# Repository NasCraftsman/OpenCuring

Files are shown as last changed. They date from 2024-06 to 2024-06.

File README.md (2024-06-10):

# OpenNixie 

</a>
</a>
</a>

Democratizing manufacturing tools is the only way to bring technological design closer to everyone. OpenCuring is the first open source resin curing machine. The first in a series of completely open manufacturing tools that will allow anyone to have their own maker lab at home.

To make this machine available to everyone, simple and affordable components have been used, such as a single and cheap PCB, a completely standard 28BYJ-48 stepper motor and an SSD1306 OLED screen. Additionally, all pieces are fully printable.

On the other hand, OpenCuring has a completely modular design, so the user can add new curing arms as needed.

There is no excuse to get your hands dirty creating!

Some of the features that the OpenCuring platform includes are:

- Wifi and BLE connected
- Modular design: it can be adapted to the user needs 
- USB Type-C for power and programming
- Up to 3A at 5V 
- 1 general pourpose button 
- 1 general pourpose potentiometer 
- 1 OLED display 
- 1 stepper motor
  
<a href="https://www.pcbway.com/project/shareproject/Open_Resin_Curing_Machine_8a6f1ecd.html">PCB from PCBWay</a>

## Multi Board Architecture

OpenCuring integrates two different pcbs: 

- <strong>Control PCB:</strong> this system includes all the user interfaces such as the OLED display, the butons and potentiometer, the USB port and all the integrated control systems. 
- <strong>Branch PCB:</strong>  this system includes the UV LEDs 

OpenCuring has been designed as a modular platform. This means that the control PCB can be connected to any UV LED PCB to adapt the system to the user's needs, playing with the wavelength and power emitted. On the other hand, the PCBs of the branches will be connected in series, allowing the user to expand the number of UV arms by adapting the system to their needs.

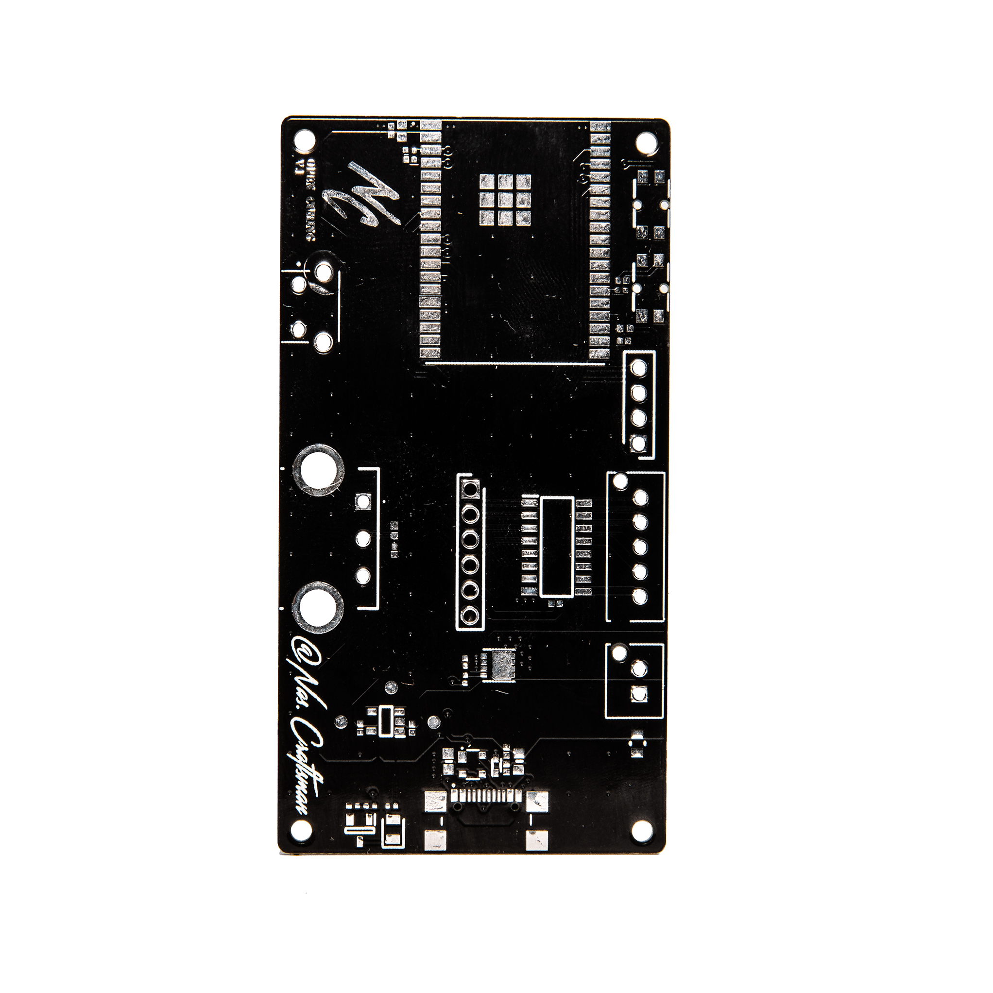
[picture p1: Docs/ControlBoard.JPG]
</a>
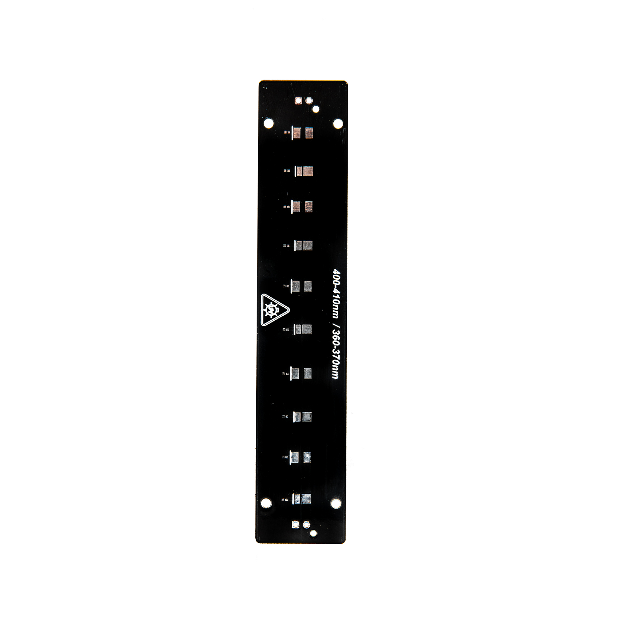
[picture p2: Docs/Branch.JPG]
</a>

## Warning

OpenCuring uses 405nm UV power LEDs, which can be hazardous to human eyesight. Please wear protective glasses or stay away from the system while the curing process is running.

## GPIOs

Function|  GPIO  | Mode
--------| ------ | -----
USB_LED | GPIO26 | Output
BUTTON  | GPIO15 | Input
POT     | GPIO36 | Input
I2C_SDA | GPIO21 | Output/Input
I2C_SCL | GPIO22 | Output
UV      | GPIO25 | Output
STEP_A1 | GPIO27 | Output
STEP_A2 | GPIO14 | Output
STEP_A3 | GPIO33 | Output
STEP_A4 | GPIO32 | Output

- The USB LED is used to indicate that a correct power source has been connected
- The button is used to start the curing process.
- The potentiometer is used to select the curing time.
- The UV pin activates a power mosfet to turn on the UV power LEDs
- STEP A1 to A4 are the control lines of the stepper motor
- The I2C bus controls the OLED display

## Board overview C3T 

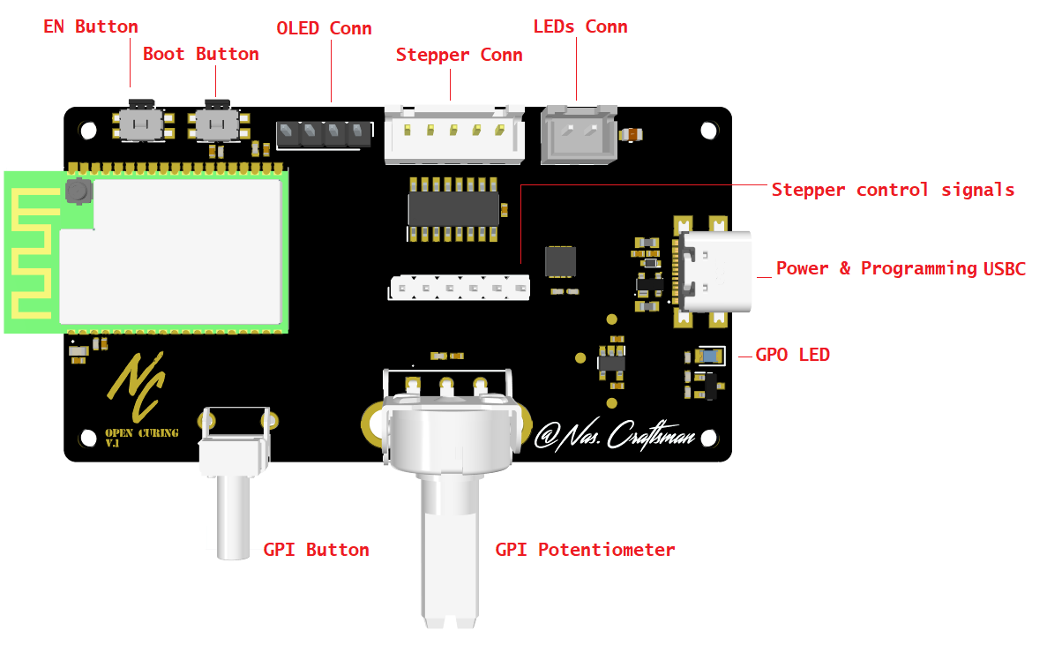
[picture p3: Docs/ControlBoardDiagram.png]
</a>

## Flashing firmware to the ESP32 

- Press and hold BOOT button while press and release EN button, then release BOOT button to enter in BOOT mode
- You can use the USB-C directly to programm the device

## Media

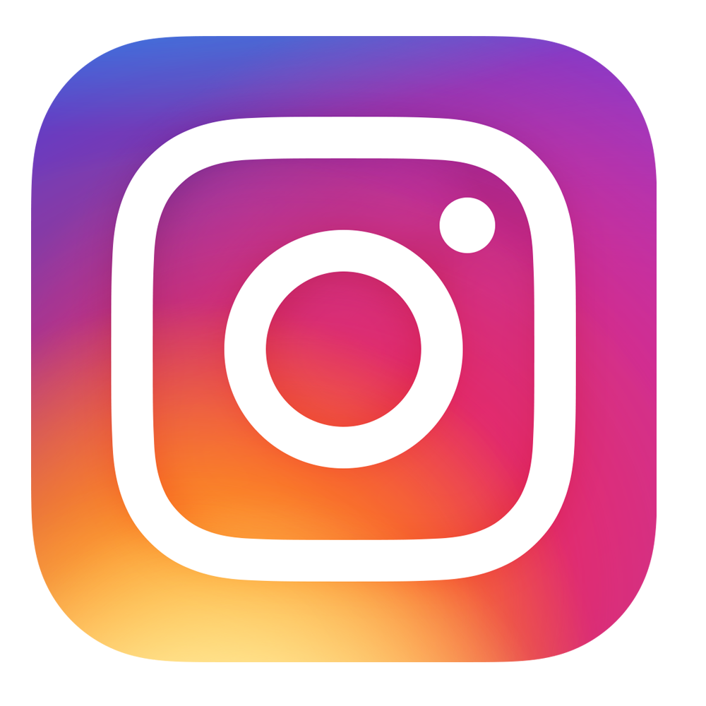
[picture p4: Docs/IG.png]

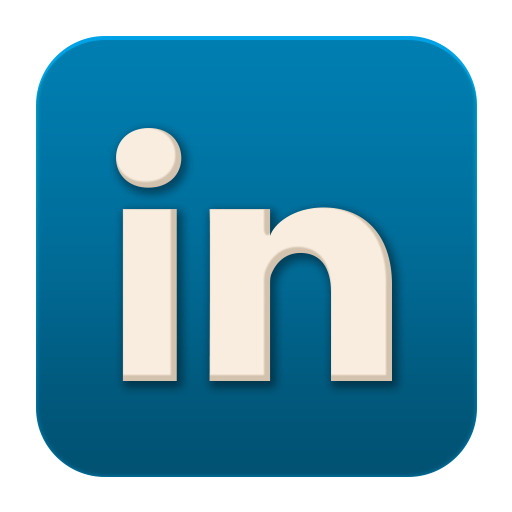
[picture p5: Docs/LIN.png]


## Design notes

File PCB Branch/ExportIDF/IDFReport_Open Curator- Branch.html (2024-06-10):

Altium customize

# IDF File Translation Report

Date: | | 26/04/2024
Time: | | 18:11:25
Elapsed Time: | | 00:00:00
PCB Filename | : | F:\NASIB\INGENIERIA\PROYECTOS\4-OPEN CURATOR\BRANCH\Open Curator- Branch.PcbDoc
IDF Board Filename | : | F:\NASIB\INGENIERIA\PROYECTOS\4-OPEN CURATOR\BRANCH\Project Outputs for Open Curator- Branch\ExportIDF\Open Curator- Branch.brd
IDF Library Filename | : | F:\NASIB\INGENIERIA\PROYECTOS\4-OPEN CURATOR\BRANCH\Project Outputs for Open Curator- Branch\ExportIDF\Open Curator- Branch.pro

Errors

Back to top

Warnings

Back to top

Save Warnings

Back to top

Save Errors

Back to top

Export Warnings

Back to top

Export Errors

Back to top

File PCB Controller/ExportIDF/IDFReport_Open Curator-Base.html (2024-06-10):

Altium customize

# IDF File Translation Report

Date: | | 26/04/2024
Time: | | 18:04:49
Elapsed Time: | | 00:00:00
PCB Filename | : | F:\NASIB\INGENIERIA\PROYECTOS\4-OPEN CURATOR\BASE\Open Curator-Base.PcbDoc
IDF Board Filename | : | F:\NASIB\INGENIERIA\PROYECTOS\4-OPEN CURATOR\BASE\Project Outputs for Open Curator-Base\ExportIDF\Open Curator-Base.brd
IDF Library Filename | : | F:\NASIB\INGENIERIA\PROYECTOS\4-OPEN CURATOR\BASE\Project Outputs for Open Curator-Base\ExportIDF\Open Curator-Base.pro

Errors

Back to top

Warnings

Back to top

Save Warnings

Back to top

Save Errors

Back to top

Export Warnings

Back to top

Export Errors

Back to top

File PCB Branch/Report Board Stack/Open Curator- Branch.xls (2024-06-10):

Board Stack Report
Stack Up |  | Layer Stack
Layer | Board Layer Stack | Name | Material | Thickness | Constant
1 |  | Top Paste
2 |  | Top Overlay
3 |  | Top Solder | Solder Resist | 0,005mm | 4,2
4 |  | Top Layer | Copper | 0,035mm
5 |  | Core | FR-4 | 1,000mm | 4,29
6 |  | Bottom Layer | Copper | 0,035mm
7 |  | Bottom Solder | Solder Resist | 0,005mm | 4,2
8 |  | Bottom Overlay
9 |  | Bottom Paste
 | Height : 1,080mm

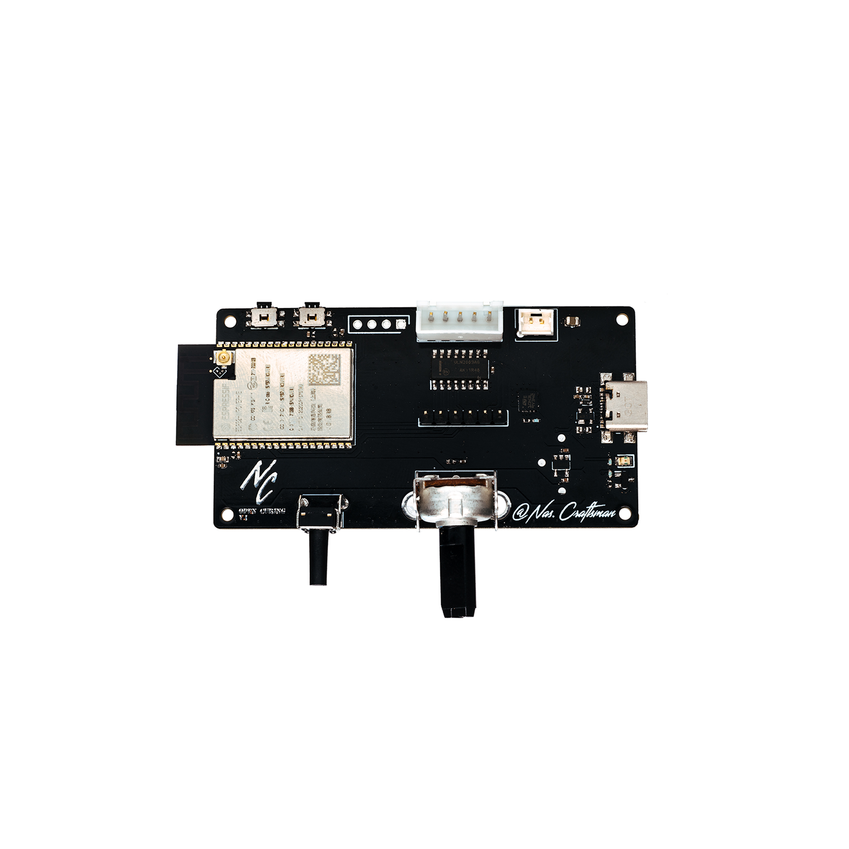
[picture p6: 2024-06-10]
Docs/OpenCuringv11.JPG

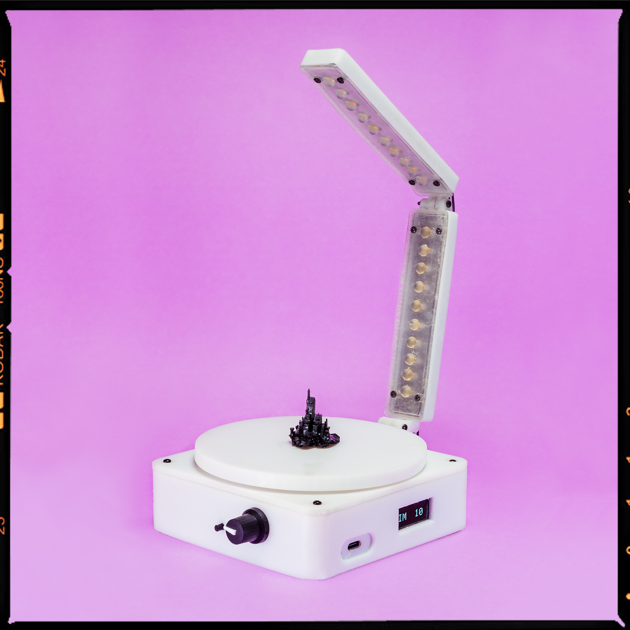
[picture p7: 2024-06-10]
Docs/_DSC4096-Edit.jpg

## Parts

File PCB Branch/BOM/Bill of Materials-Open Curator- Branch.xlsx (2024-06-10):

Designator | Value | Description | Quantity | Part Number | Manufacturer | DNP
J100, J101 |  | Connector | 2 | B2B-XH-AM(LF)(SN) | JST (JAPAN SOLDERLESS TERMINALS)
L100, L101, L102, L103, L104 |  | SMD UV Clear Non-Diff 405nm | 5 | VLMU3100-GS08 | Vishay
L105, L106, L107, L108, L109 |  | SMD UV Clear Non-Diff 405nm | 5 | 153283367A212 | Wurth Elektronik
R100, R101, R102, R103, R104 | 60 | SMD 59 Ohms 62.5 mW 0402 1% | 5 | RC0402FR-0759RL | Yageo
R105, R106, R107, R108, R109 | 24 | SMD 24 Ohms 62.5 mW 0402 5% | 5 | RC0402JR-0724RL | Yageo

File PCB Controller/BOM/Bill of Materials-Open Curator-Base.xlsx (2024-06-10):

Designator | Value | Description | Quantity | Part Number | Manufacturer | DNP
C100 | 10nF | 0.01 uF 16 VDC 20% 0402 X7R | 1 | GRM155R71C103MA01D | Murata
C101, C102, C104, C105, C109, C110, C112, C113 | 100nF | CAP, MLCC, 0402/1005, 25V, X7R, | 8 | GRM155R71E104KE14D | Murata
C103 | 22uF | CAP CER 22UF 6.3V X5R 0603 | 1 | GRM188R60J226MEA0D | Murata
C106, C107 | 1uF | 1.0uF 16V 10% 0402 X5R | 2 | GRM155R61C105KA12D | Murata
C108 | 22uF | 0805 35VDC 22uF 20% X5R 1.25mm | 1 | C2012X5R1V226M125AC | Murata
C111 | 4.7uF | 4.7uF 10V 20% 0402 X5R | 1 | GRM155R61A475MEAAD | Murata
D100 |  | ESD / TVS diode 12-pF, +/-5.5V, +/-30-kV ESD protection diode in 0402 and SOD-523 package | 1 | TPD1E10B06DYAR | Texas Instruments
D101 |  | LED | 1 | 597-3305-607F | Dialight
D102 |  | ESD Diode | 1 | PRTR5V0U2X | Nexperia
FB100, FB101 |  | Ferrite Bead, 2A @ 100MHz, 120ohms 25% | 2 | ILHB0603ER121V | Vishay
J100 |  | Connector | 1 | USB4110-GF-A | GCT (GLOBAL CONNECTOR TECHNOLOGY)
J101 |  | Connector | 1 | B2B-XH-AM(LF)(SN) | JST (JAPAN SOLDERLESS TERMINALS)
J102 |  | Connector | 1 | G800W302018EU | Amphenol Communications Solutions
J103 |  | Connector | 1 | B5B-XH-AM (LF)(SN) | JST (JAPAN SOLDERLESS TERMINALS)
J104 |  | Connector | 1 | PH1-04-UA | Adam Tech
P100 |  | Pot 12mm 5Kohm | 1 | P120K-F20BR5K | TT Electronics
Q100 |  | MOSFET N-channel 30 V 0.015 Ohm 9A STripFET V | 1 | STL10N3LLH5 | STMicroelectronics
Q102 |  | MOSFET (N-Channel) | 1 | NX7002AKVL | Nexperia
R100, R101, R108 | 100 | RES SMD 100 OHM 1% 1/16W 0402 | 3 | MCS04020D1000BE000 | Vishay
R102, R107, R110, R111 | 100k | 100 kOhms 62.5mW 0402 1% | 4 | RC0402FR-07100KL | Yageo
R103, R104 | 10k | RES SMD 10K OHM 1% 1/16W 0402 | 2 | SFR01MZPF1002 | Stackpole Electronics Inc
R105 | 1k | RES SMD 1K OHM 1% 1/16W 0402 | 1 | CRT0402-FZ-1001GST | Yageo
R106 | 22.1k | RES SMD 22.1K OHM 1% 1/16W 0402 | 1 | RT0402BRE0722K1L | Stackpole Electronics Inc
R109 | 47.5k | RES SMD 47.5K OHM 1% 1/16W 0402 | 1 | RN731ETTP4752F50 | Stackpole Electronics Inc
S100 |  | Connector | 1 | 2-1825027-0 | TE Connectivity
S101, S102 |  | button | 2 | 436331045822 | Wurth Elektronik
U100 |  | 700mA High Speed LDO Regulator | 1 | XC6210B332MR-G | Torex
U101 |  | Wi-Fi - 802.11 SMD Module ESP32-WROVER-IE, ESP32-D0WD-V3, 3.3V 64Mbit PSRAM, 16 MB SPI flash, IPEX connector | 1 | ESP32-WROVER-IE(M213EH2864UH3Q0) | Espressif Systems
U102 |  | DARLINGTON TRNS ARRY | 1 | ULN2003ADR2G | onsemi
U103 |  | USB to UART Bridge QFN24 | 1 | CP2102N-A02-GQFN24R | Silicon Labs

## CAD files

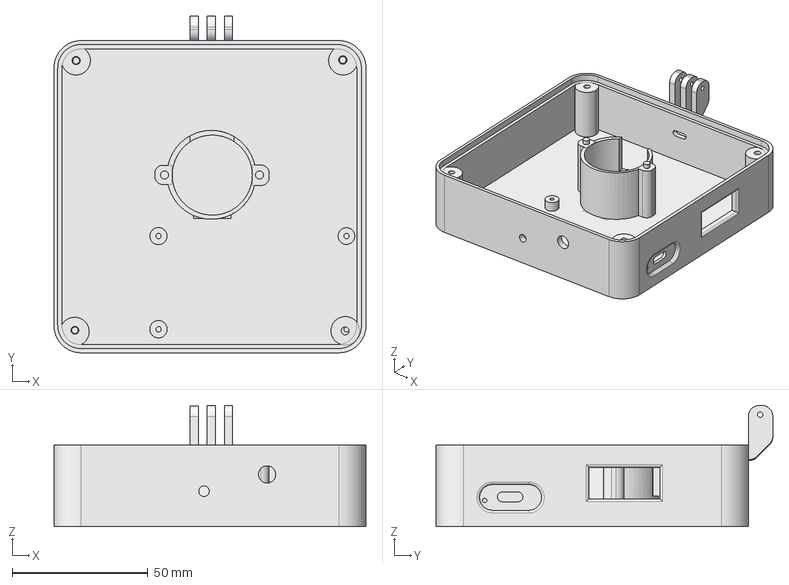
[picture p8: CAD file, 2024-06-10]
Case/Body.step
114.9 x 124.0 x 44.6 mm

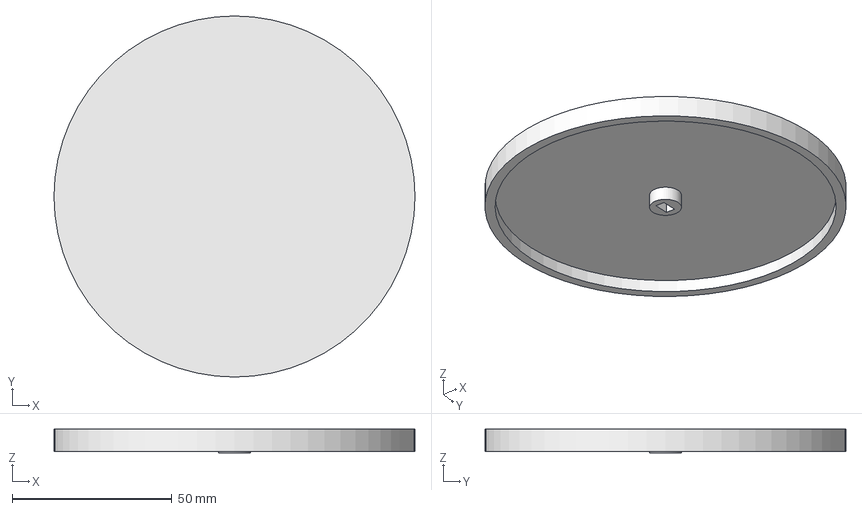
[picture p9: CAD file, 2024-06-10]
Case/Platform.step
112.8 x 112.8 x 7.40 mm

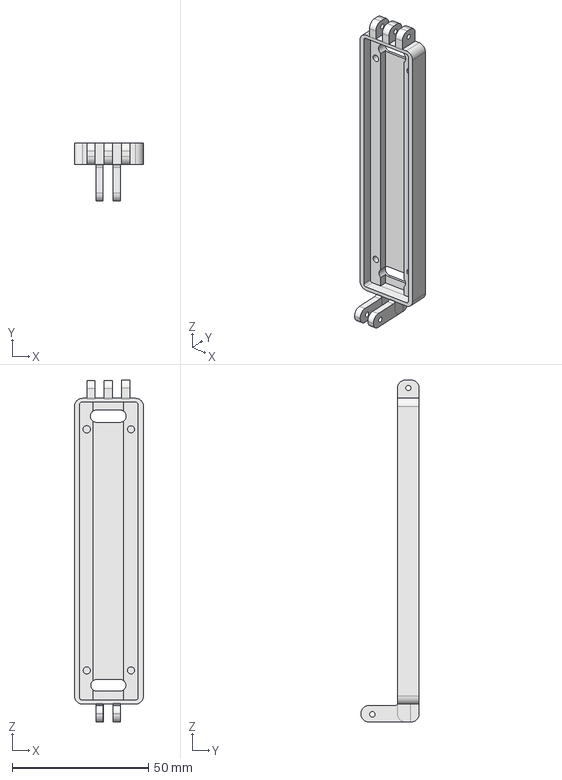
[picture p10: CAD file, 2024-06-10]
Case/Branch_Vertical_Base.step
25.4 x 21.5 x 125.7 mm

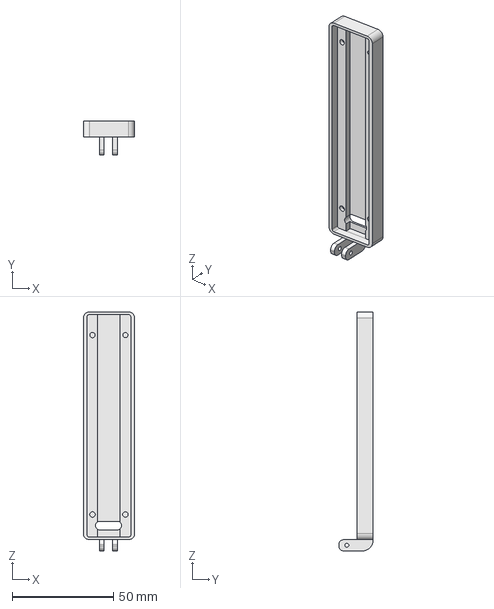
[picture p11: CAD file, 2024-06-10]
Case/Branch_Horizontal_Base.step
25.4 x 17.0 x 118.1 mm

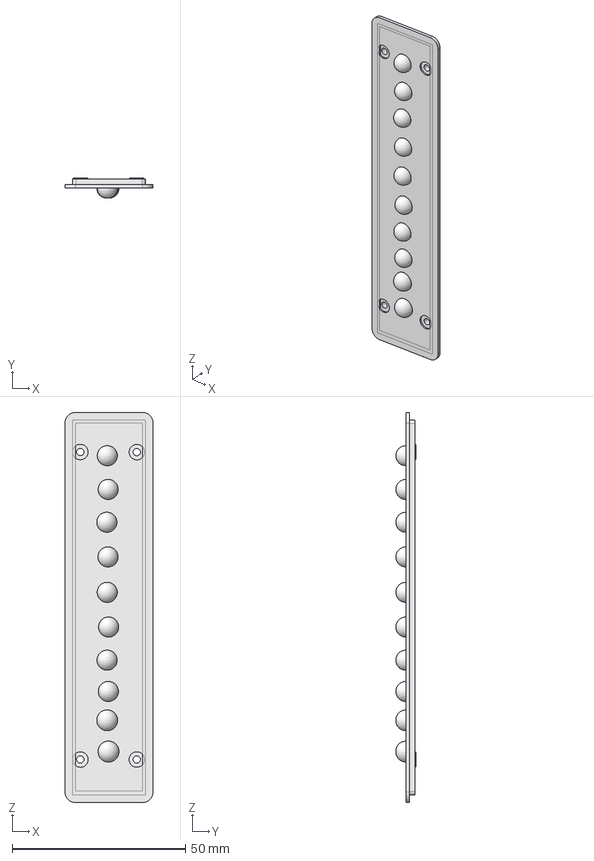
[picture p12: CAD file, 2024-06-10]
Case/Branch_Vertical_Lid.step
25.4 x 5.90 x 112.4 mm

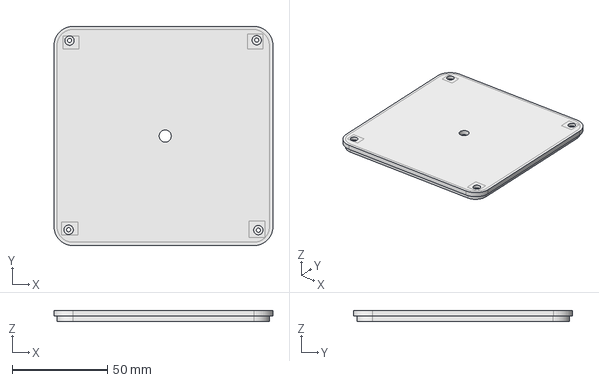
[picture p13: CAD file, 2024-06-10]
Case/Lid.step
114.9 x 115.0 x 6.00 mm

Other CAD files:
Case/Branch_Horizontal_Lid.step
PCB Branch/ExportSTEP/Open Curator- Branch.x_t

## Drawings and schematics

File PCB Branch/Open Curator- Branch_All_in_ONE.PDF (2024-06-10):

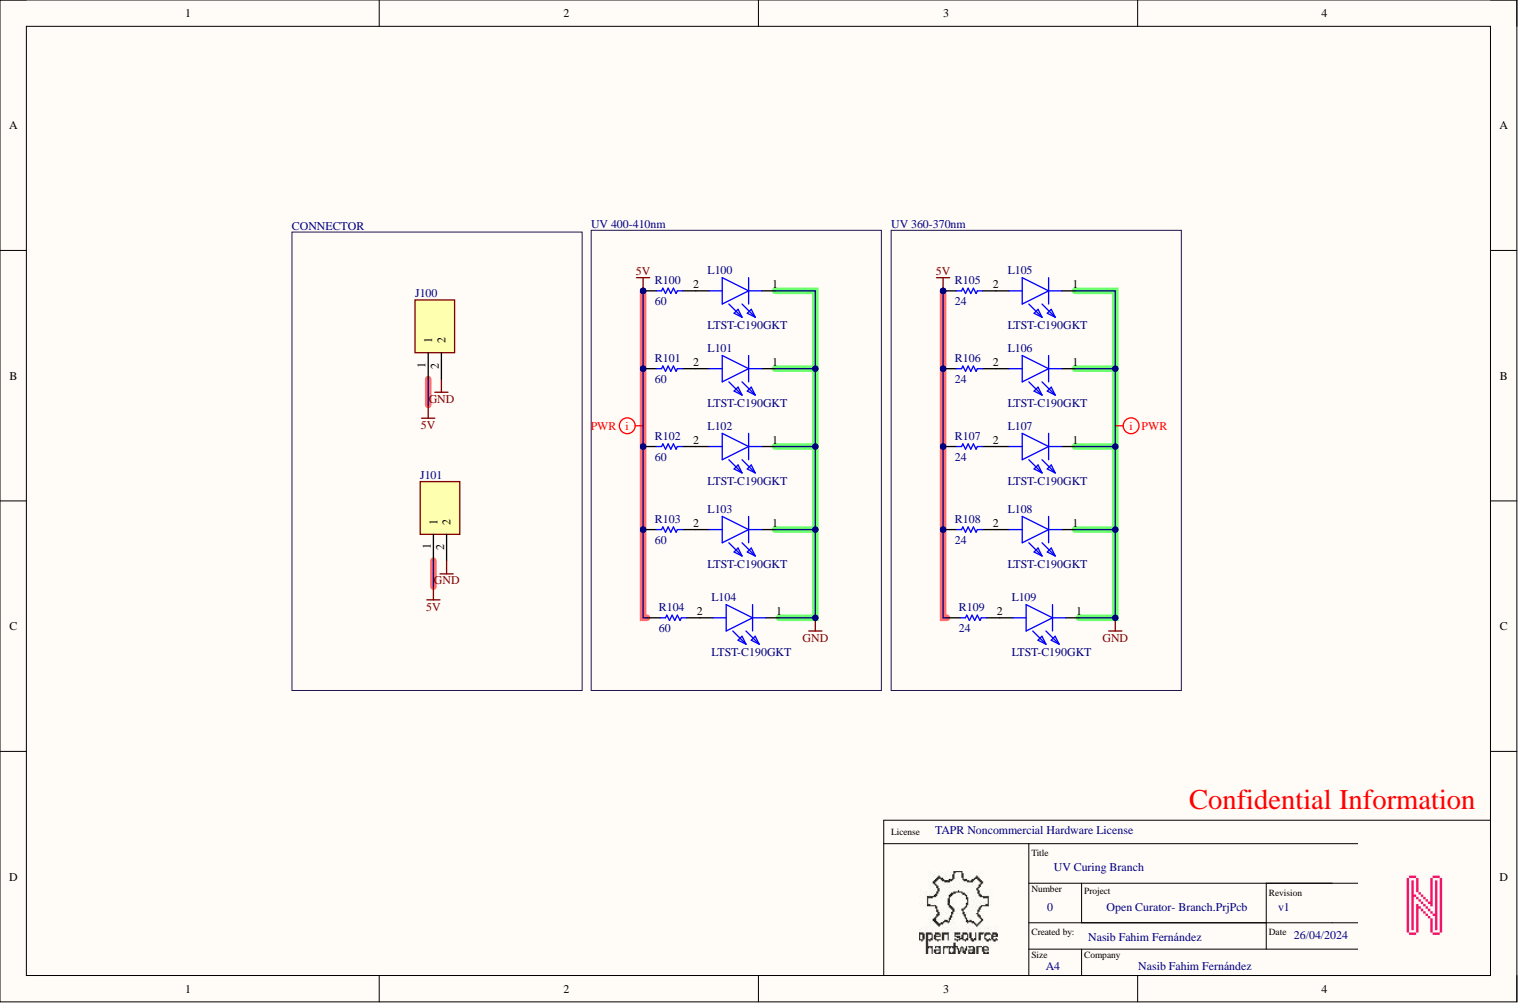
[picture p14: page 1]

Title UV Curing Branch

Number 0 | Project Open Curator- Branch.PrjPcb | Revision v1

Created by: Nasib Fahim Fernández | | Date 26/04/2024

Company

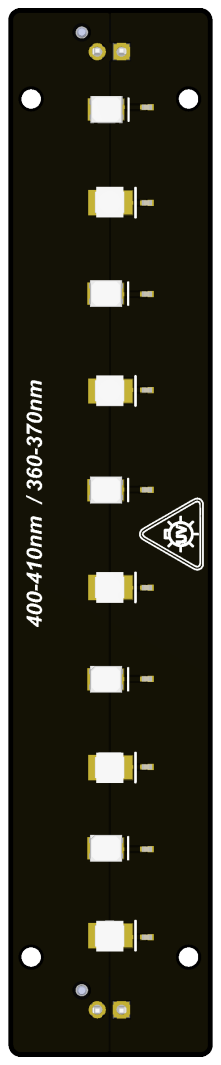
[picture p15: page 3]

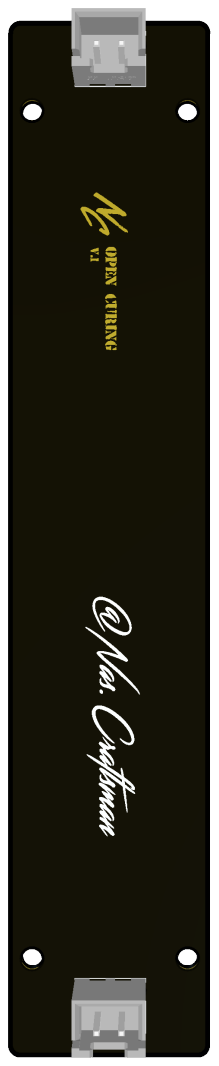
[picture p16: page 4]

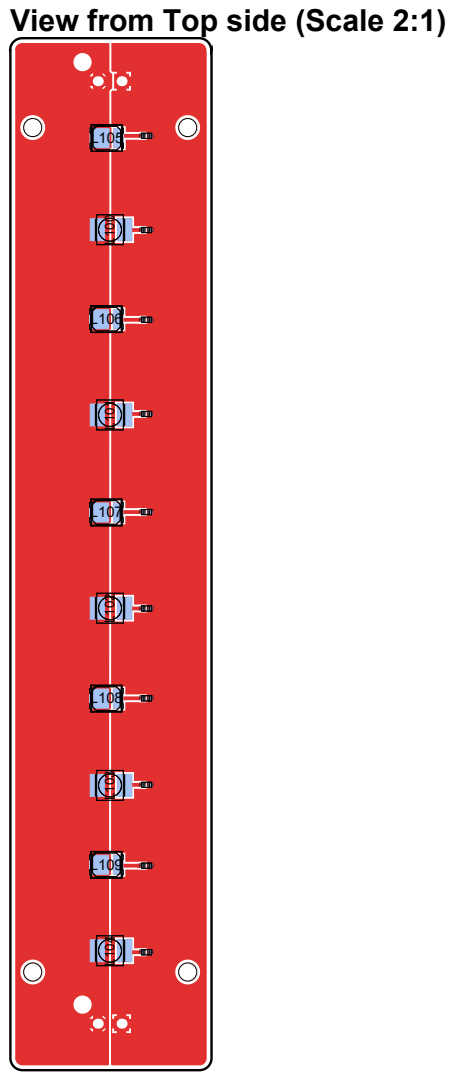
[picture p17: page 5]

View from Top side (Scale 2:1)

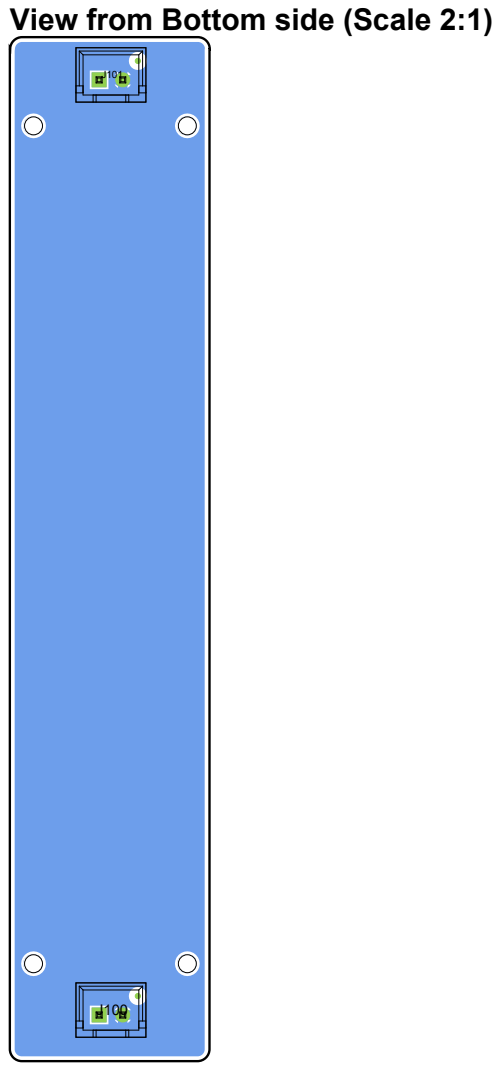
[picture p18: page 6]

View from Bottom side (Scale 2:1)

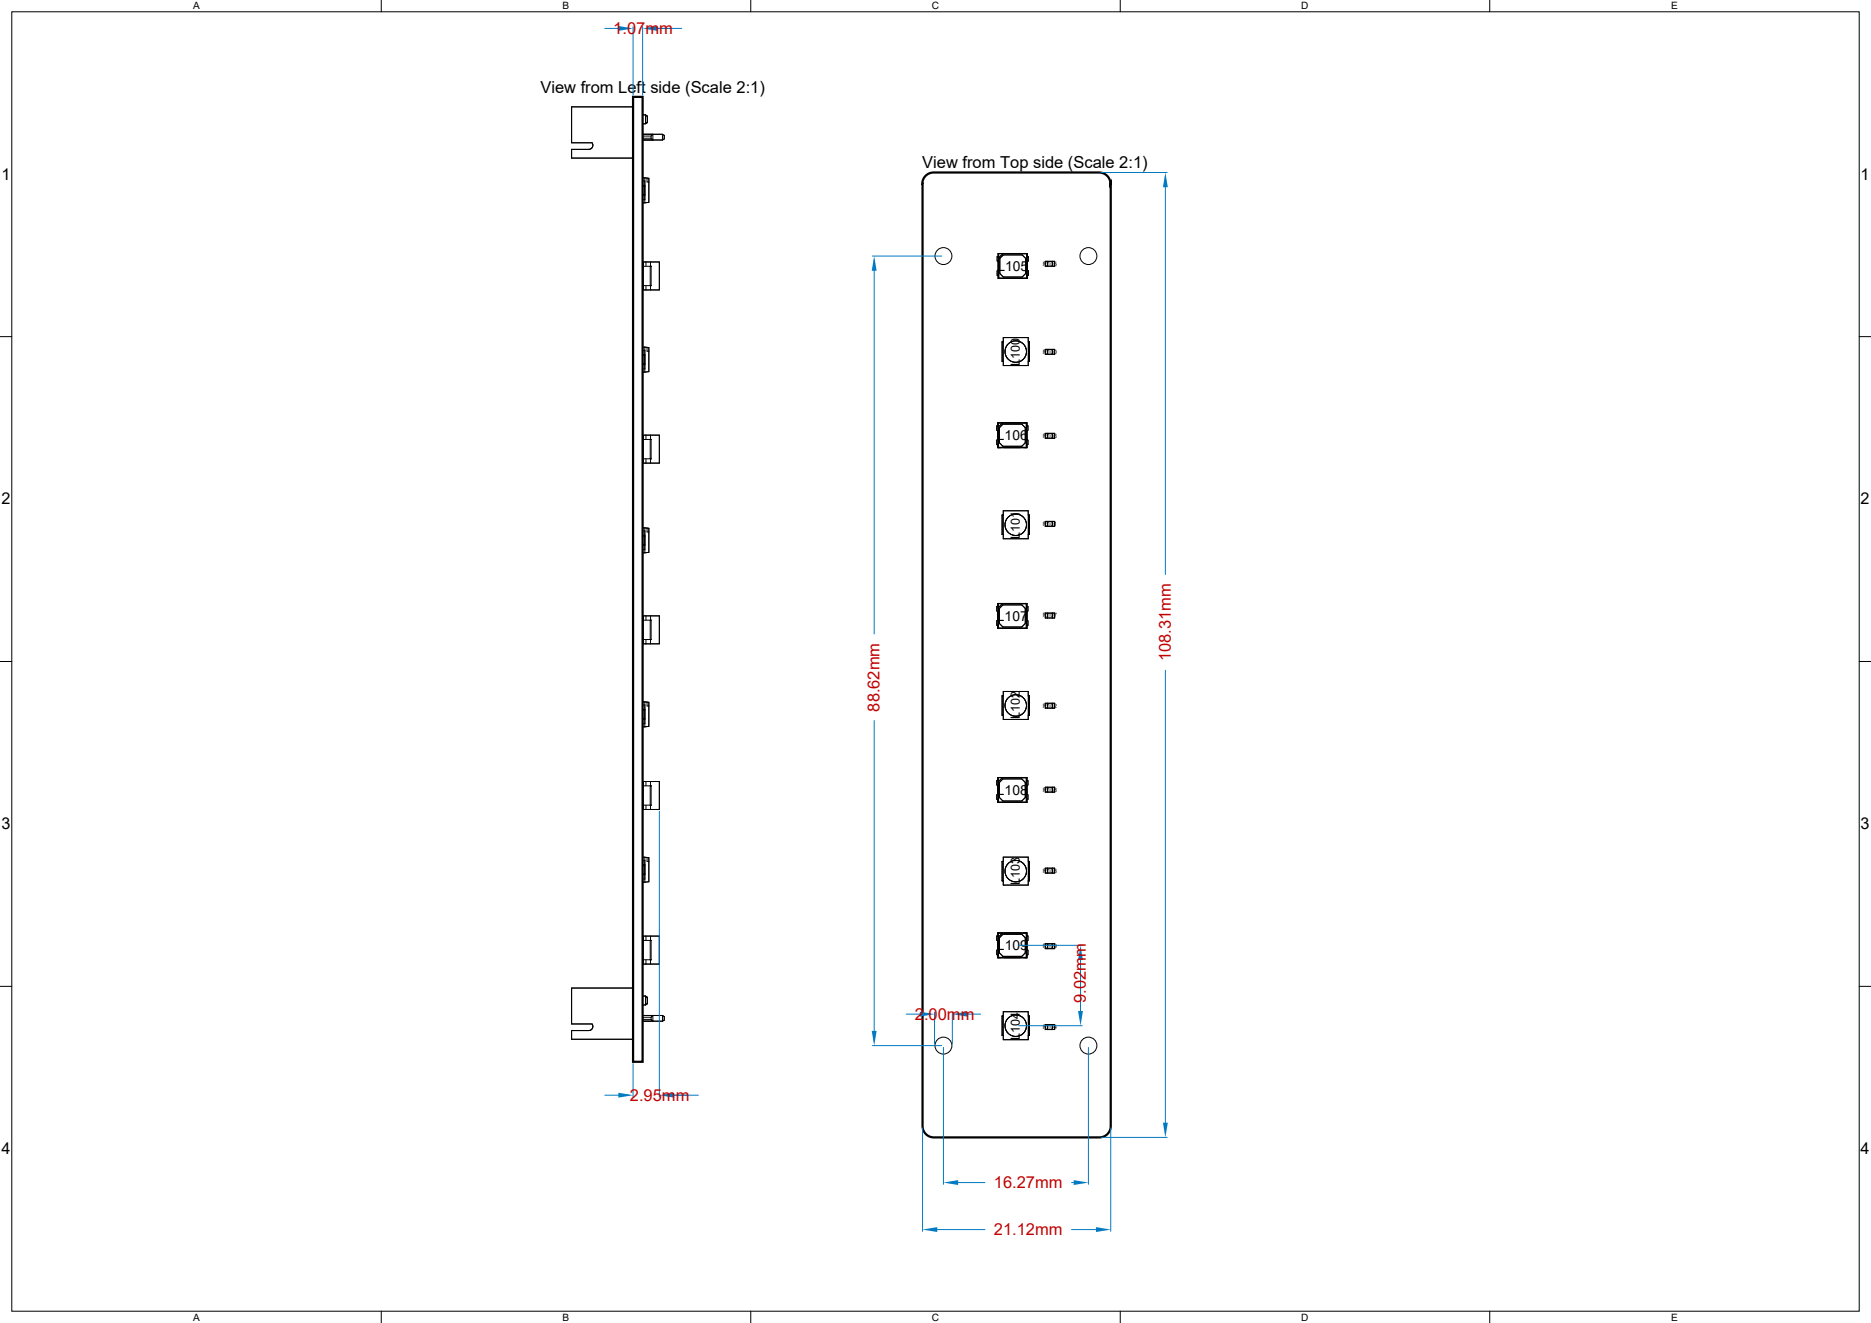
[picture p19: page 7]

View from Left side (Scale 2:1)

View from Top side (Scale 2:1)

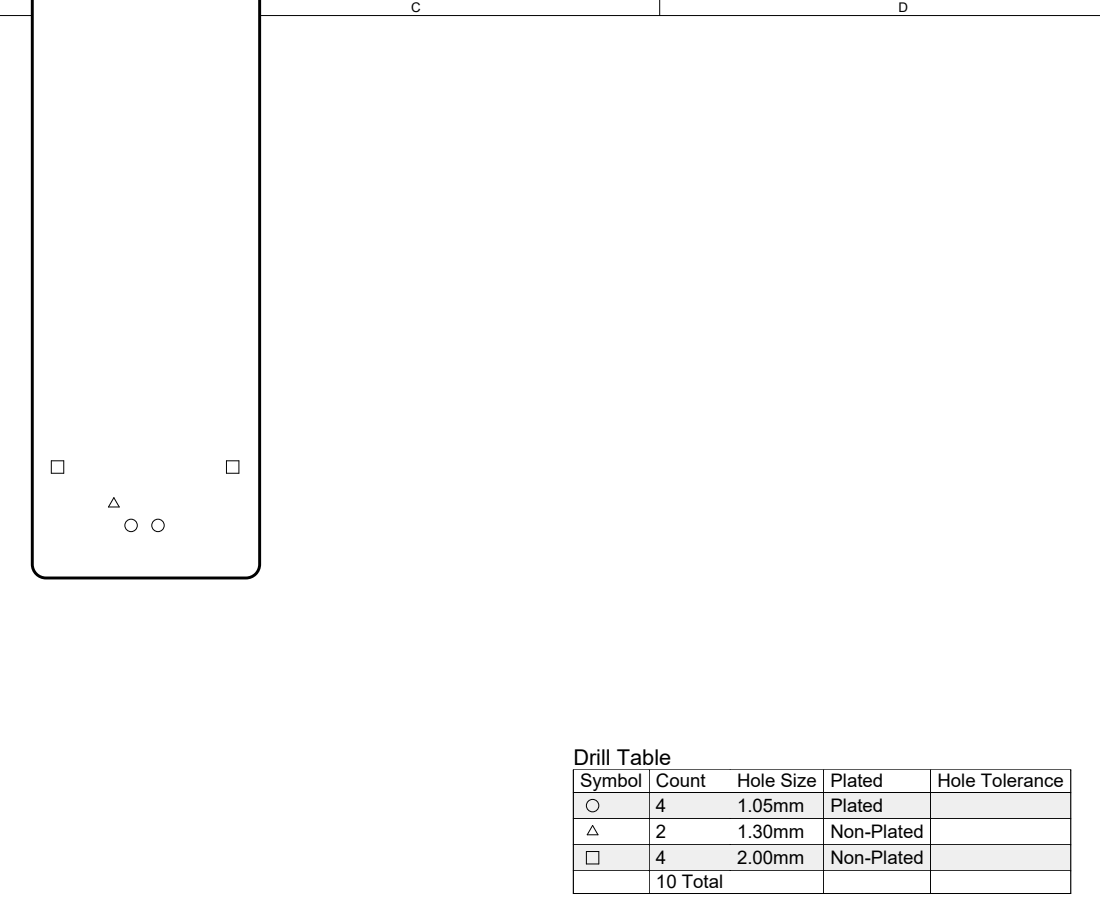
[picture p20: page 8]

Symbol | Count | Hole Size | Plated | Hole Tolerance

4 | 1.05mm | Plated
2 | 1.30mm | Non-Plated
4 | 2.00mm | Non-Plated
10 Total

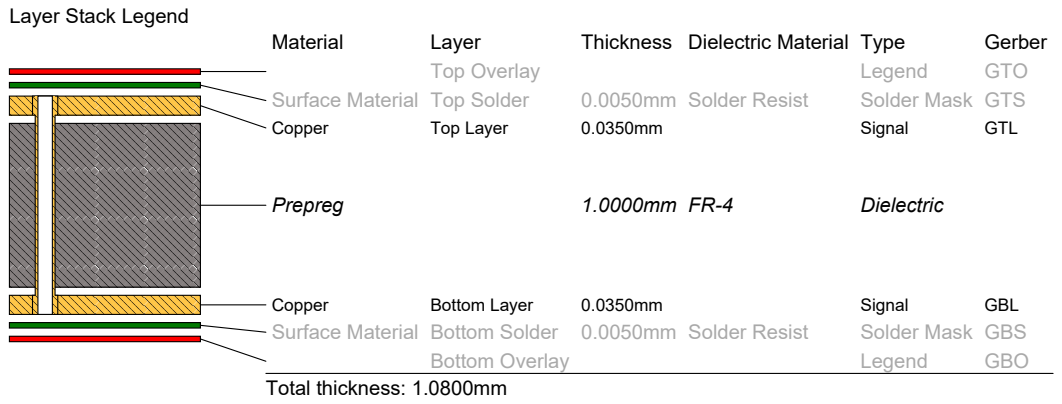
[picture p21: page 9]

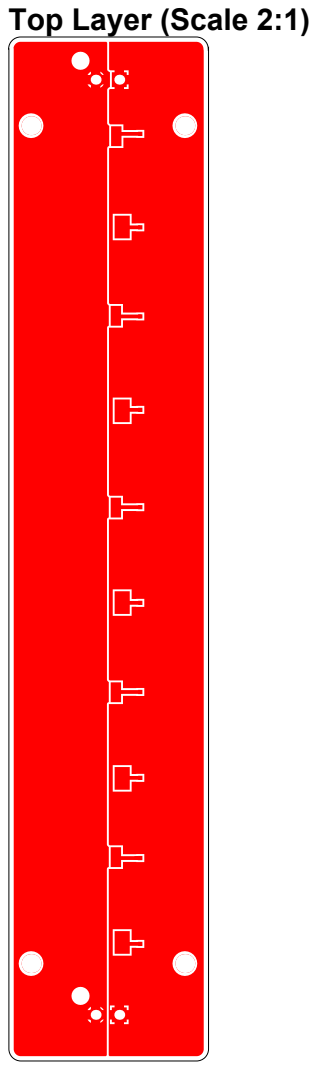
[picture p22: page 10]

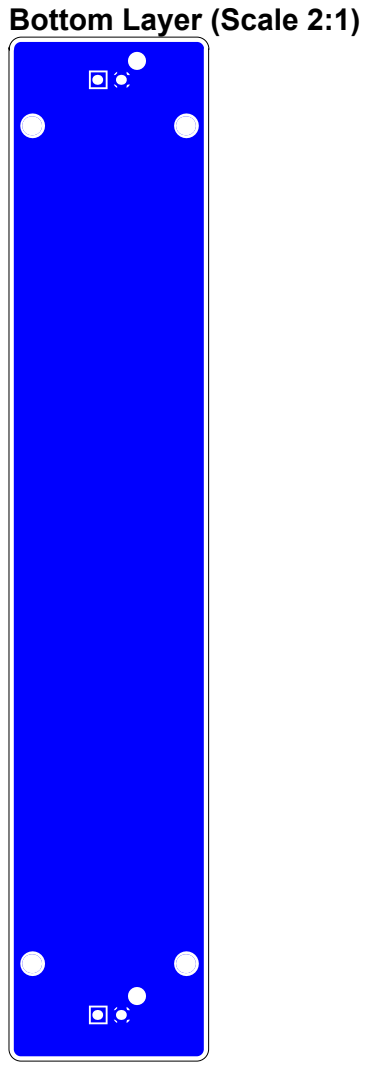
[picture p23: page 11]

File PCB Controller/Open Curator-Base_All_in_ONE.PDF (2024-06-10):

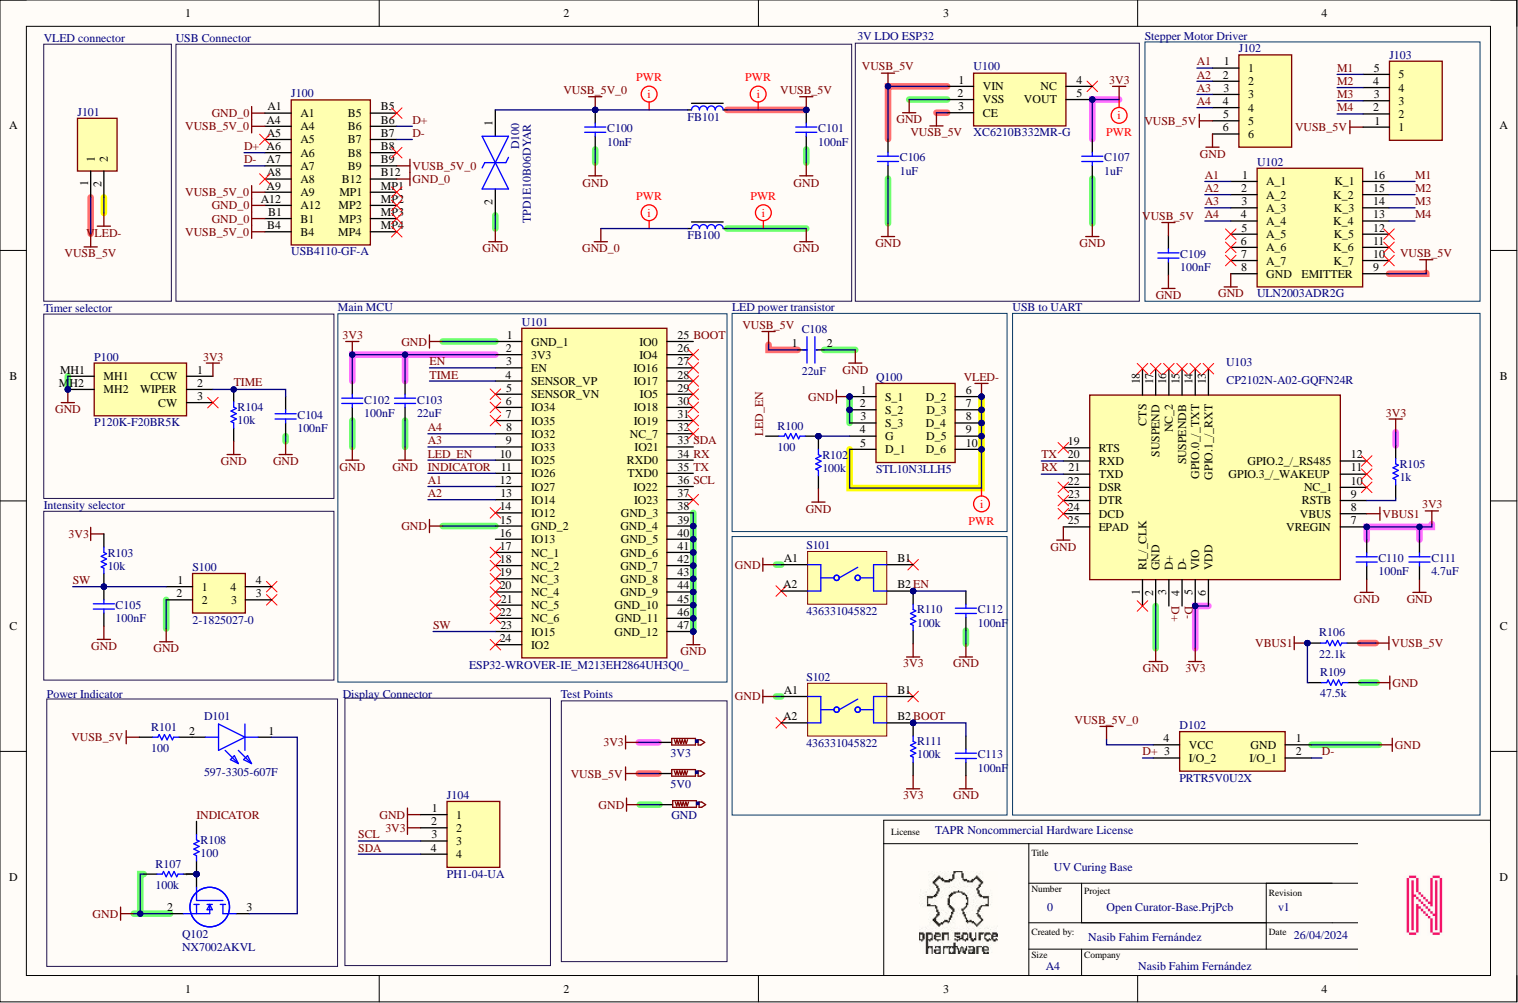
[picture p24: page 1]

Title UV Curing Base

Number 0 | Project Open Curator-Base.PrjPcb | Revision v1

Created by: Nasib Fahim Fernández | | Date 26/04/2024

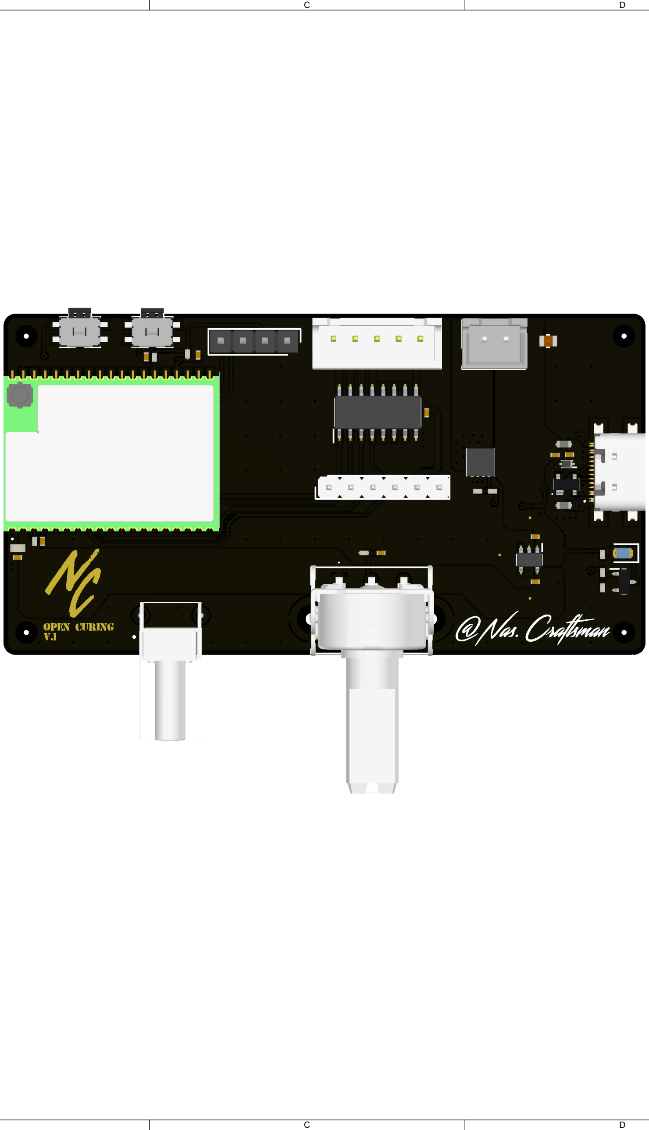
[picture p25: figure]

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


View from Top side (Scale 5:2)


View from Bottom side (Scale 5:2)



Drill Drawing View (Scale 1.8318)

Symbol | Count | Hole Size | Plated | Hole Tolerance

112 | 0.30mm | Plated
2 | 0.65mm | Non-Plated
4 | 0.75mm | Non-Plated
2 | 0.99mm | Plated
8 | 1.00mm | Plated
2 | 1.05mm | Plated
4 | 1.10mm | Plated
6 | 1.20mm | Plated
2 | 1.30mm | Non-Plated
2 | 1.30mm | Plated
4 | 2.00mm | Non-Plated
2 | 3.44mm | Plated
150 Total




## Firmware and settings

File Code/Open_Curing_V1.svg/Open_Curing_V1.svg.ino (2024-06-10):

//////////////////////////////////////////////////////////////////////////////////////////////////////////////////////
//
//  OPEN CURING
//
//  The circuit:
//  * This code is made to be used with the Open Curing Controller V1
//
//  The License: 
//  * Created in 2024 by nas.craftsman https://github.com/NasCraftsman
//  * This example code is in the public domain.
//
//////////////////////////////////////////////////////////////////////////////////////////////////////////////////////
#define LED      26      // General purpose LED
#define BUT      15      // General purpose button
#define POT      36      // General purpose Potentiometer
#define UV       25      // Control pin for UV LEDs

#define A1       27      // Stepper motor A1
#define A2       14      // Stepper motor A2
#define A3       33      // Stepper motor A3
#define A4       32      // Stepper motor A4

#define OLED_WIDTH 128 // OLED display width,  in pixels
#define OLED_HEIGHT 32 // OLED display height, in pixels



#include <TinyStepper_28BYJ_48.h>
#include <Wire.h>
#include <Adafruit_GFX.h>
#include <Adafruit_SSD1306.h>

bool button=false, go=false;
double potentiometer=0;
const int STEPS_PER_REVOLUTION = 2048;
int state=0,vel=0,power=0,tim=0; 
String states[1]={"TIM  "};
String cowntdown[11]={"  10   ","   9   ","   8   ","   7   ","   6   ","   5   ","   4   ","   3   ","   2   ","   1   ","  GO!!   "};

TinyStepper_28BYJ_48 stepper;
Adafruit_SSD1306 oled(OLED_WIDTH, OLED_HEIGHT, &Wire, -1);


void read_UI(){
  if(!digitalRead(BUT)& !button){
    button=true;
    state++;
    if(state>0){
      state=0; 
      go=true;
    }
    Serial.print("Button Pressed! Menu:");
    Serial.println(state);
  }
  if(digitalRead(BUT)){
    button=false;
  }
  potentiometer=100-((analogRead(POT)-2450)*100)/1645; 
}

void print_Display(){
   oled.clearDisplay();          // clear display
   oled.setTextSize(3);          // text size
   oled.setTextColor(WHITE);     // text color
   oled.setCursor(0, 10);        // position to display
   oled.print(states[state]);    // text to display
   if(state==0){
      oled.print(tim);
      tim=potentiometer/3;
   }
   else if(state==1){
      oled.print(vel);
      vel=potentiometer/10;
   }
   else if(state==2){
      oled.print(power);
      power=potentiometer/10;
   }
   else{
    
   }
   oled.display();               
}
void curing(){
   Serial.println("Starting count down...");
   for(int x=0; x<11; x++){
      oled.clearDisplay();                // clear display
      oled.setTextSize(3);                // text size
      oled.setTextColor(WHITE);           // text color
      oled.setCursor(0, 10);              // position to display
      oled.println(cowntdown[x]);                   // text to display
      oled.display();  
      delay(1000);
      Serial.println(cowntdown[x]);
   }
   Serial.println("Starting curing process...");
   Serial.print("Speed: ");
   Serial.println(vel);
   Serial.print("Power: ");
   Serial.println(power);
   Serial.print("Timer: ");
   Serial.println(tim);
   
   oled.clearDisplay();                
   oled.println("UV ON!!");
   oled.display();  
   delay(1000);delay(1000);
   digitalWrite(UV, HIGH);
   stepper.setSpeedInStepsPerSecond(2048/(11-vel));
   stepper.setAccelerationInStepsPerSecondPerSecond(512);
   stepper.moveRelativeInSteps(60*tim*(2048/(11-vel))); 
   digitalWrite(UV, LOW); 
   oled.clearDisplay();
   oled.setTextSize(3);                
   oled.setTextColor(WHITE);     
   oled.println("DONE");
   oled.display();
   delay(1000);
   go=false;
}

void setup() {
   Serial.begin(115200);
   Serial.println("---------------------SETTING UP----------------------");
   pinMode(LED, OUTPUT);
   pinMode(UV, OUTPUT);
   pinMode(BUT, INPUT);
   stepper.connectToPins(A1, A2, A3, A4);
   if (!oled.begin(SSD1306_SWITCHCAPVCC, 0x3C)) {
      Serial.println(F("SSD1306 allocation failed"));
      while (true);
    }
   //oled.rotation=3;
   Serial.println("-----------------------------------------------------");
   digitalWrite(LED, HIGH);
   oled.clearDisplay();                // clear display
   oled.setTextSize(3);                // text size
   oled.setTextColor(WHITE);           // text color
   oled.setCursor(0, 10);              // position to display
   oled.println("HELLO!");                   // text to display
   oled.display();  
   delay(1000);
}

void loop() {
  read_UI();
  if(go){ //start Curing 
      curing();
  }
  print_Display();
}
